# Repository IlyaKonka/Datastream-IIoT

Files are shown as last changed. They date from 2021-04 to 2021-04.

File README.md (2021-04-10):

# Data Stream Processing in IIoT environments
## Video demonstration
[](https://youtu.be/aPCmk4RJr00)
## Video description
At the top of the video you can see log output of IIoT-System.
There is vibration visualisation in the right corner and live video of the lego prototype in the left corner.<br>
<br>
<br>
Timecodes:
* (0:00 — 0:30) start of IIoT-System
* (0:30 — 0:52) response of **identification module** to the lego part without id tag 
* (0:54 — 2:53) production workflow of **defect 1** lego part 
* (1:30 — 1:45) demonstration of predictive maintenance
* (2:56 — 4:40) production workflow of **non-defective** lego part
* (4:45 — 5:00) transport to the **drop zone** the lego part which has already been processed

## Sensor simulators
You can start the docker project with vibration/color sensor simulator(s).
There is more information in the **IIoT-System** folder.

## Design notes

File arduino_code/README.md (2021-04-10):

# Arduino code
## Getting Started
Before use install libraries from libraries.7z

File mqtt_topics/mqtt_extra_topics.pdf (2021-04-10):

Loading

Topic | Type | Payload | Description
/tables/connection | Publish | arduinoLoadingTable|connected arduinoRollingTable|connected arduinoQualityTable|connected arduinoColourSensor|connected arduinoUnloadingTable|connected | Info about connection of the arduinos.
/loading/loopTime | Publish | {timeMillis} | Time of the main loop.
/loading/motorInfo | Publish | isStarted|{ value } direction|{value} speed|{value} | Info about motor. isStarted: 0 or 1 direction: l or r speed: (0,255)
/loading/info | Publish | isStarted|{ value } direction|{value} speed|{value} loopTime|{value} action|{value} DoneMsg | Info about table if something was changed. isStarted(motor): 0 or 1q direction: l or r speed: (0,255) loopTime: 0 or 1 action: F or D DoneMsg: “ Rolling is done.”
/loading/warning | Publish | Some warnings | If something wrong, Arduino sends a msg
/loading/rfidReadProblem | Publish | Msg with info about movement of the material. (a lit bit right or left) | If rfid reader cannot read a tag, this msg will be sent.
/loading/control | Subscribe | {t} – loop time (on/off) {i} – motorInfo {s} – start motor {p} – pause motor {r} – direction right {l} – direction left {number} – speed (0,255) | Extra control of the table. (GodMode)

Rolling

Topic | Type | Payload | Description
/rolling/loopTime | Publish | {timeMillis} | Time of the main loop.
/rolling/motorInfo | Publish | isStarted|{ value } isRollingStarted|{value} direction|{value} rollingDirection|{value} speed|{value} rollingSpeed|{value} | Info about motor. isStarted: 0 or 1 isRollingStarted| 0 or 1 direction: l or r rollingDirection: l or r speed: (0,255) rollingSpeed: (0,255)
/ rolling /info | Publish | isStarted|{ value } isRollingStarted|{value} direction|{value} rollingDirection|{value} speed|{value} rollingSpeed|{value} loopTime|{value} DoneMsg | Info about table if something was changed. isStarted(motor): 0 or 1 direction: l or r speed: (0,255) loopTime: 0 or 1
/ rolling /warning | Publish | Some warnings | If something wrong, Arduino sends a msg
/ rolling /control | Subscribe | {t} – loop time (on/off) {i} – motorInfo {s} – start motor {p} – pause motor {m} – start roll {z} – pause roll {r} – direction right (automatically for roll direction) {l} – direction left (automatically for roll direction) {number} – speed (0,255) (automatically for roll speed) | Extra control of the table. (GodMode)

Quality

Topic | Type | Payload | Description
/quality/loopTime | Publish | {timeMillis} | Time of the main loop.
/quality/motorInfo | Publish | isStarted|{ value } direction|{value} speed|{value} | Info about motor. isStarted: 0 or 1 direction: l or r speed: (0,255)
/quality/info | Publish | isStarted|{ value } direction|{value} speed|{value} loopTime|{value} DoneMsg | Info about table if something was changed. isStarted(motor): 0 or 1 direction: l or r speed: (0,255) loopTime: 0 or 1
/ quality /warning | Publish | Some warnings | If something wrong, Arduino sends a msg
/ quality /control | Subscribe | {t} – loop time (on/off) {i} – motorInfo {s} – start motor {p} – pause motor {r} – direction right {l} – direction left {number} – speed (0,255) | Extra control of the table. (GodMode)

ColourSensor

Topic | Type | Payload | Description
/ colourSensor/warning | Publish | Some warnings | If something wrong, Arduino sends a msg

Unloading

Topic | Type | Payload | Description
/unloading/loopTime | Publish | {timeMillis} | Time of the main loop.
/unloading/motorInfo | Publish | isStarted|{ value } direction|{value} speed|{value} TurnedOut|{value} | Info about motor. isStarted: 0 or 1 direction: l or r speed: (0,255) TurnedOut: 0 or 1 (position of turnout system [0 is start pos])
/ unloading /info | Publish | isStarted|{ value } direction|{value} speed|{value} loopTime|{value} TurnedOut|{value} DoneMsg | Info about table if something was changed. isStarted(motor): 0 or 1 direction: l or r speed: (0,255) loopTime: 0 or 1 TurnedOut: 0 or 1 (position of turnout system [0 is start pos])
/ unloading /warning | Publish | Some warnings | If something wrong, Arduino sends a msg
/ unloading /control | Subscribe | {t} – loop time (on/off) {i} – motorInfo {s} – start motor {p} – pause motor {r} – direction right {l} – direction left {number} – speed (0,255) {f} – turn out forward {b} – turn out back | Extra control of the table. (GodMode)

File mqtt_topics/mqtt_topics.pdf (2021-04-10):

### 1.1 Loading

### 1.1.1 MQTT messages

Name | P/S | Topic | Payload | QoS | Lvl | Description
ReadyToNewMat | Publish | /loading/ReadyToNewMat | String “ready” | 0 | 3 | Sends the messages if it is ready for the new material part. (interval 0.5 s)
MatLoaded | Publish | /loading/MatLoaded | String {MAT_ID} | 0 | 3 | Is send when a material is placed on the Roller Table and the RFID reader reads it. Contains the id of the material.
MatPosition | Publish | /loading/MatPosition | String {MAT_ID}|{MAT_POS} | 0 | 3 | Sends position of the material all the time when it is on the table.
MatLoadingInfo | Publish | /rolling/ MatLoadingInfo | String {MAT_ID} | 0 | 2 | Sends id if material is ready to roll.
MatDropped | Publish | /loading/ MatDropped | String {MAT_ID} | 0 | 3 | Msg after dropping.
MatProcess | Subscribe | /loading/MatProcess | String {MAT_ID}|F or {MAT_ID}|D | 1 | 3 | Waits for a message with the command from the server. There are two commands. “Forwarding” or “Dropping “.
MatReadyToRoll | Subscribe | /loading/MatReadyToRoll | String {MAT_ID} | 0 | 2 | Waits for the message from the rolling table (1.2) that it is ready.

### 1.2 Rolling

### 1.2.1 MQTT messages

Name | P/S | Topic | Payload | QoS | Lvl | Description
MatReadyToRoll | Publish | /loading/MatReadyToRoll | String {MAT_ID} | 0 | 2 | Sends the messages if it is ready for the new material part.
MatPosition | Publish | /rolling /MatPosition | String {MAT_ID}|{ MAT_POS} | 0 | 3 | Sends position of the material all the time when it is on the table.
RollQuery | Publish | /rolling / RollQuary | String {MAT_ID} | 0 | 3 | Sends id of material (before rolling).
MatRollInfo | Publish | /quality / MatRollInfo | String {MAT_ID} | 0 | 2 | Sends id if material is ready to quality check.
MatAfterRoll | Publish | rolling/ MatAfterRoll | String {MAT_ID} | 0 | 3 | Msg after roll
RollThickness | Subscribe | /rolling/ RollThickness | String {MAT_ID}|{ MAT_THKN SS} | 1 | 3 | After RollQuery server sends info about thickness of the material. Then it can be rolled in some mode of the roller table.
MatLoadingInfo | Subscribe | /rolling/ MatLoadingInfo | String {MAT_ID} | 0 | 2 | Waits for the message with information about id. (from Loading Table) Then motor is started and transport material to the “Roll”.
MatReadyToQCh eck | Subscribe | /rolling/ MatReadyToQCheck | String {MAT_ID} | 0 | 2 | Waits for the message from the quality table (1.3) that it is ready.

### 1.3 Quality

### 1.3.1 MQTT messages

Name | P/S | Topic | Payload | QoS | Lvl | Description
MatReadyToQCheck | Publish | /rolling/MatReadyToQCheck | String {MAT_ID} | 0 | 2 | Sends the messages if it is ready for the new material part.
MatPosition | Publish | /quality/MatPosition | String {MAT_ID}|{M AT_POS} | 0 | 3 | Sends position of the material all the time when it is on the table.
MatReadyToQCheck | Publish | / quality / MatReadyToQCheck | String {MAT_ID} | 0 | 2/3 | Sends the message to server (colour sensor) when the material is in the “quality check place”.
MatQualityInfo | Publish | /unloading/MatQualityInfo | String {MAT_ID} | 0 | 2 | Sends id if material is ready to unloading.
MatRollInfo | Subscribe | /quality/ MatRollInfo | String {MAT_ID} | 0 | 2 | Waits for the message with information about id. (from Rolling Table) Then motor is started and transport material to the colour sensor.
MatCheck | Subscribe | /quality/ MatCheck | String {MAT_ID}|{RS LT} | 0 | 2/3 | Waits for server callback with result of qcheck. After the signal the material will be moved to the end of the quality table.
MatReadyToUnloading | Subscribe | /quality/MatReadyToUnloading | String {MAT_ID} | 0 | 2 | Waits for the message from the unloading table (1.4) that it is ready.
MatMove | Subscribe | /quality/MatMove | String {MAT_ID} | 0 | 2 | Waits for the message from the colour sensor (if it is connected) and then move material forward and back to detect a defect.

### 1.3.2 Colour Sensor

Name | P/S | Topic | Payload | QoS | Lvl | Description
MatCheck | Publish | /colourSensor/MatCheck | String {MAT_ID}| | 0 | 3 | Sends byte arr. Size=400 First 8 byte is id of mat (ascii) Then r,g,b [0,255] If it is not enough time for colour sensor to fill all arr, it fills automatically with 0.
MatMove | Publish | /quality/MatMove | String {MAT_ID}|s {MAT_ID}|e | 0 | 2 | Sends msg to the quality table that the material should be moved. (to detect little defects) at first s (start pos) And then e (end pos)
MatReadyToQCheck | Subscribe | /colourSensor/MatReadyToQCh eck | String {MAT_ID} | 0 | 3 | Waits for the message from the server then start communication with quality table.
StartAutoQCheck | Subscribe | /colourSensor/StartAutoQCheck | String {MAT_ID} | 0 | 2 | Waits for the msg from quality table and only then colour sensor works.
MatEndQCheck | Subscribe | /colourSensor/MatEndQCheck | String {MAT_ID} | 0 | 2 | Waits for the message from the quality table that the moving of material is finished, then colour sensor stops.

Unloading

### 1.3.3 MQTT messages

Name | P/S | Topic | Payload | QoS | Lvl | Description
MatReadyToUnlo ading | Publish | /quality/ MatReadyToUnloading | String {MAT_ID} | 0 | 2 | Sends the messages if it is ready for the new material part.
MatPosition | Publish | /unloading/MatPosition | String {MAT_ID}|{ MAT_POS} | 0 | 3 | Sends position of the material all the time when it is on the table.
MatFinal | Publish | /unloading/ MatFinal | String {MAT_ID} | 0 | 3 | Sends when the material is finally handled and transported.
MatQuery | Publish | /unloading/ MatQuery | String {MAT_ID} | 0 | 3 | Sends id of material (before rolling).
MatDrop | Subscribe | /unloading/MatDrop | String {MAT_ID}|1 or {MAT_ID}|0 | 1 | 3 | Waits for the message (after MatQuery) from the server with information about quality test. If it is ok, then continue rolling. If not, it will be turned out.
MatQualityInfo | Subscribe | /unloading/MatQualityIn fo | String {MAT_ID} | 0 | 2 | Waits for the message with information about id. (from Quality Table) Then motor is started and transport material to the “Turn out”.

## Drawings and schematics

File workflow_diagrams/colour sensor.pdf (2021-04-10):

# Colour Sensor

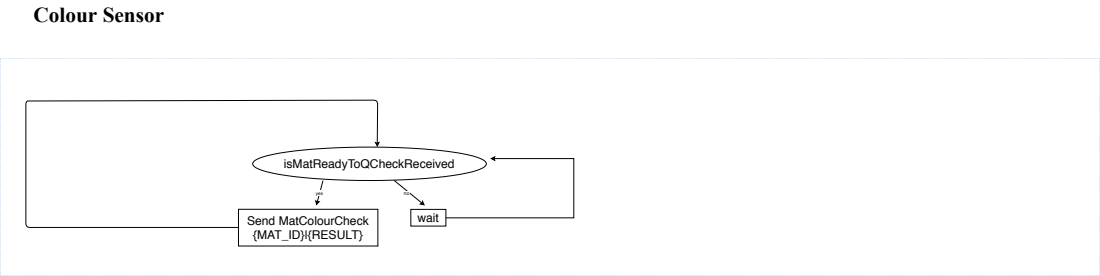
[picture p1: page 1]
isMatReadyToQCheckReceived; yes; Send MatColourCheck; wait; {MAT_ID}|{RESULT}

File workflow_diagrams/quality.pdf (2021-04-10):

# 3) Quality

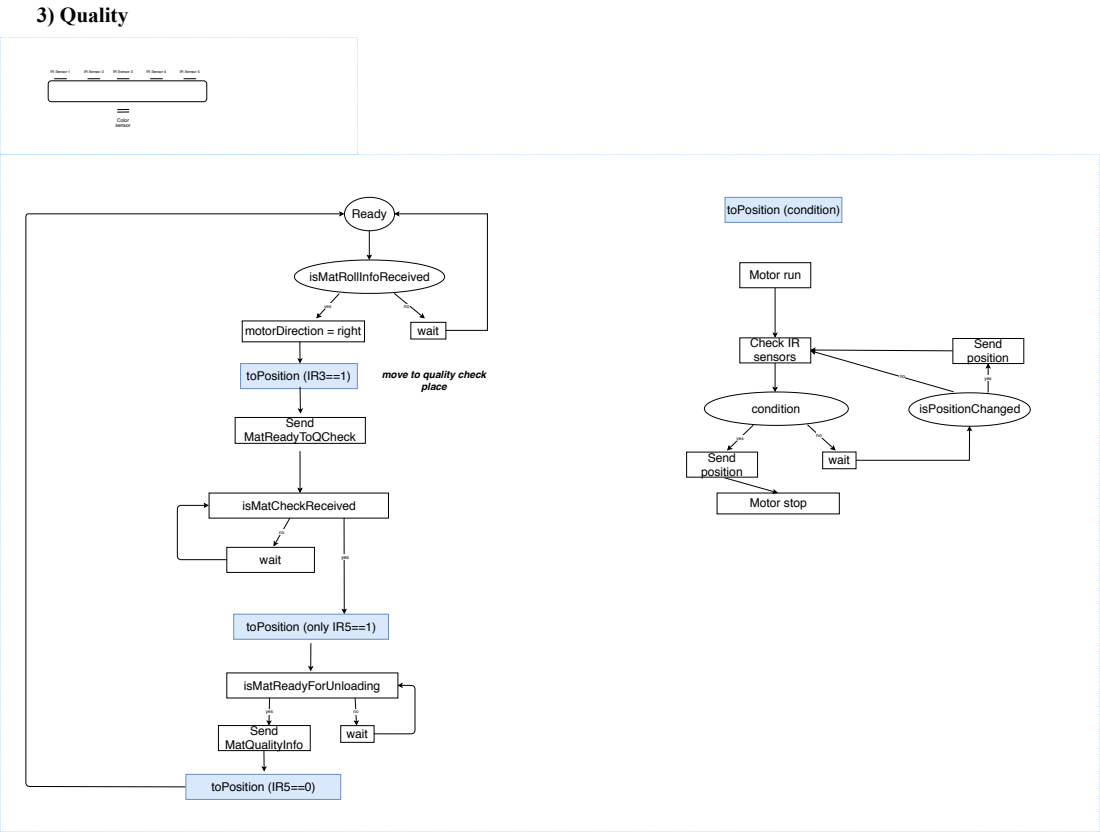
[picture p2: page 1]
IR Sensor 1; IR Sensor 2; IR Sensor 3; IR Sensor 4; IR Sensor 5; Ready; isMatRollInfoReceived; yes; wait; isMatReadyForUnloading; Color sensor; motorDirection = right; Send MatQualityInfo; Motor run; Motor stop; Check IR sensors; condition; Send position; isPositionChanged; toPosition (condition); toPosition (IR3==1); move to quality check; place; toPosition (only IR5==1); toPosition (IR5==0); isMatCheckReceived; yes wait; Send MatReadyToQCheck

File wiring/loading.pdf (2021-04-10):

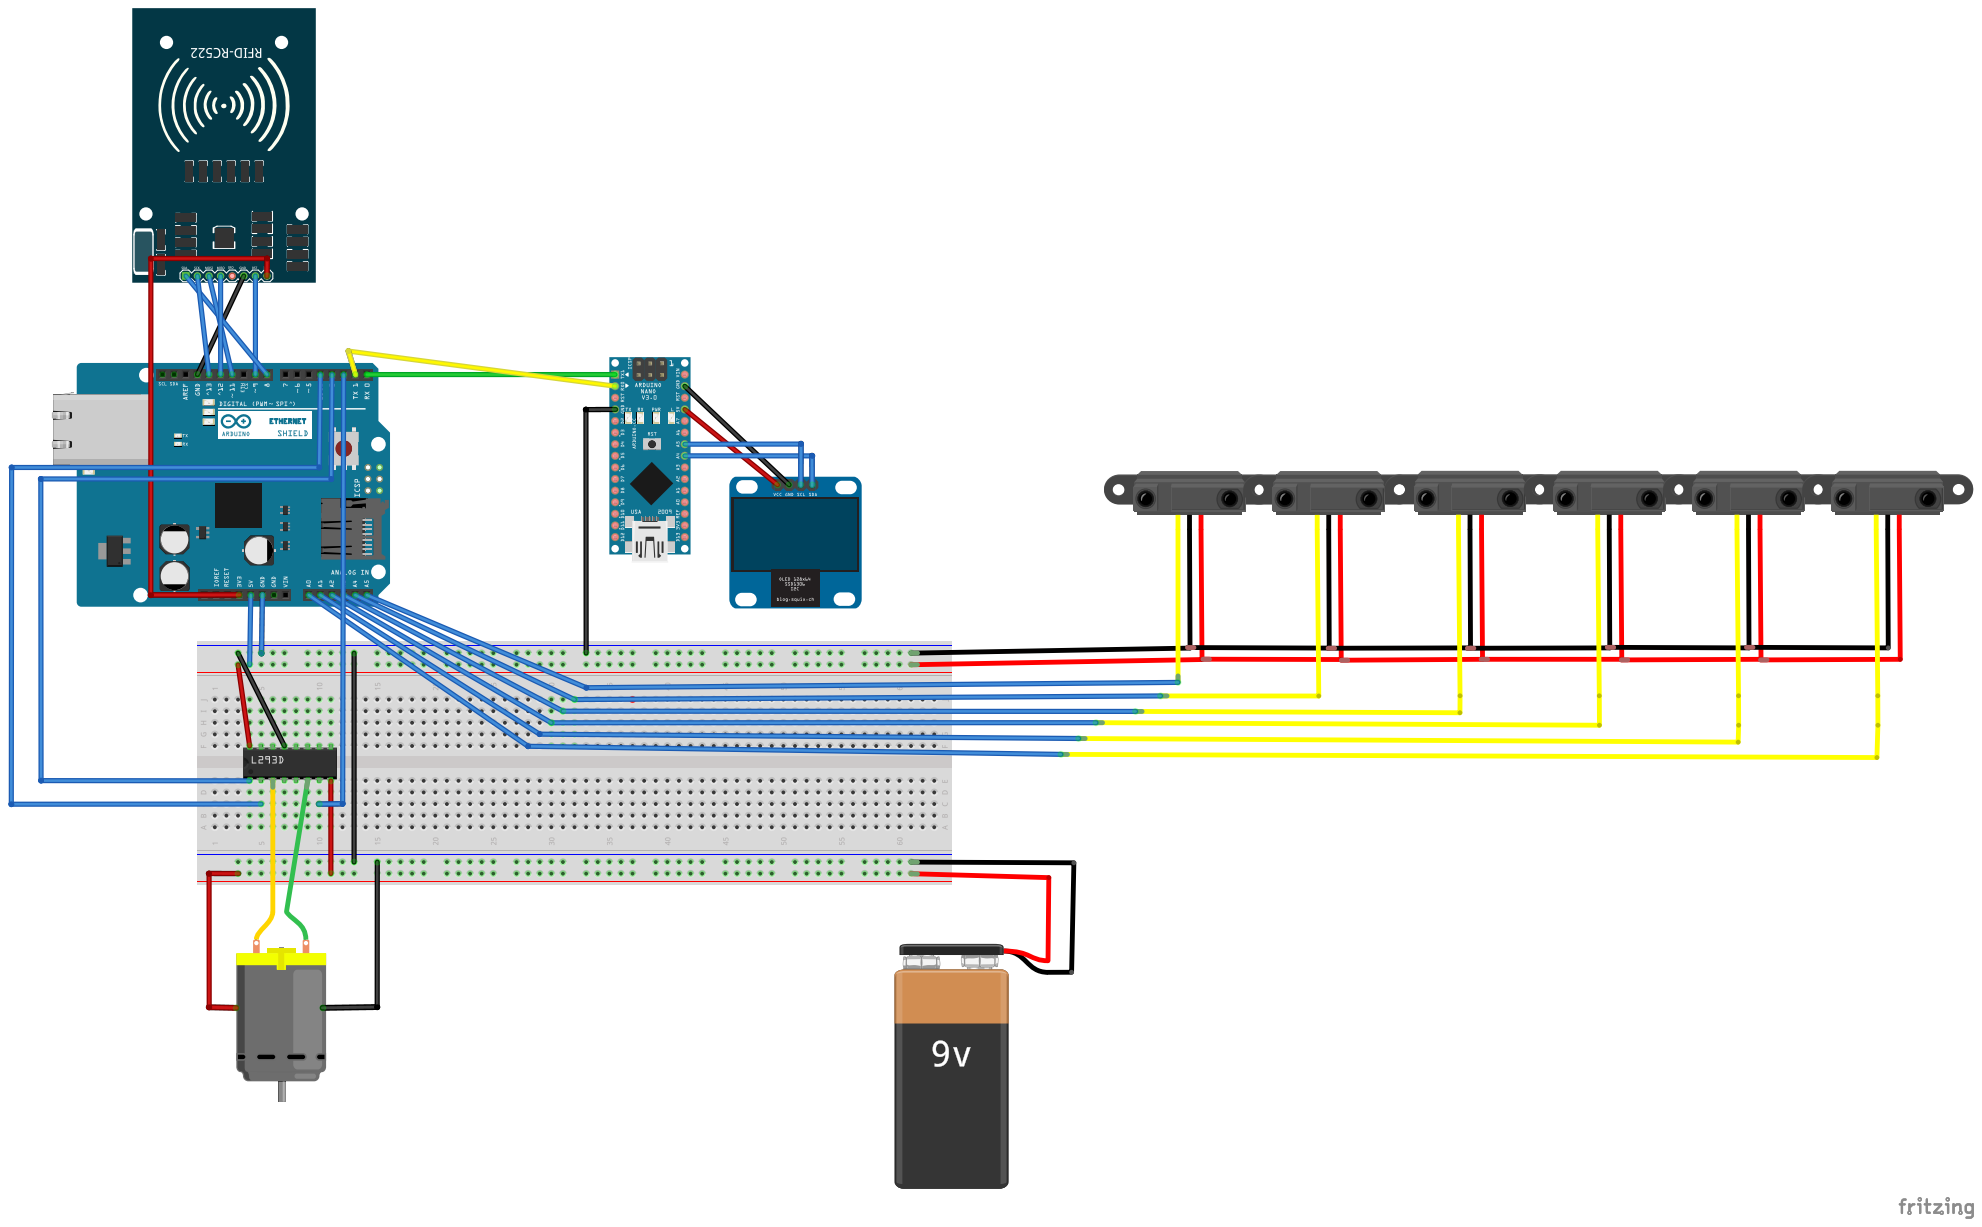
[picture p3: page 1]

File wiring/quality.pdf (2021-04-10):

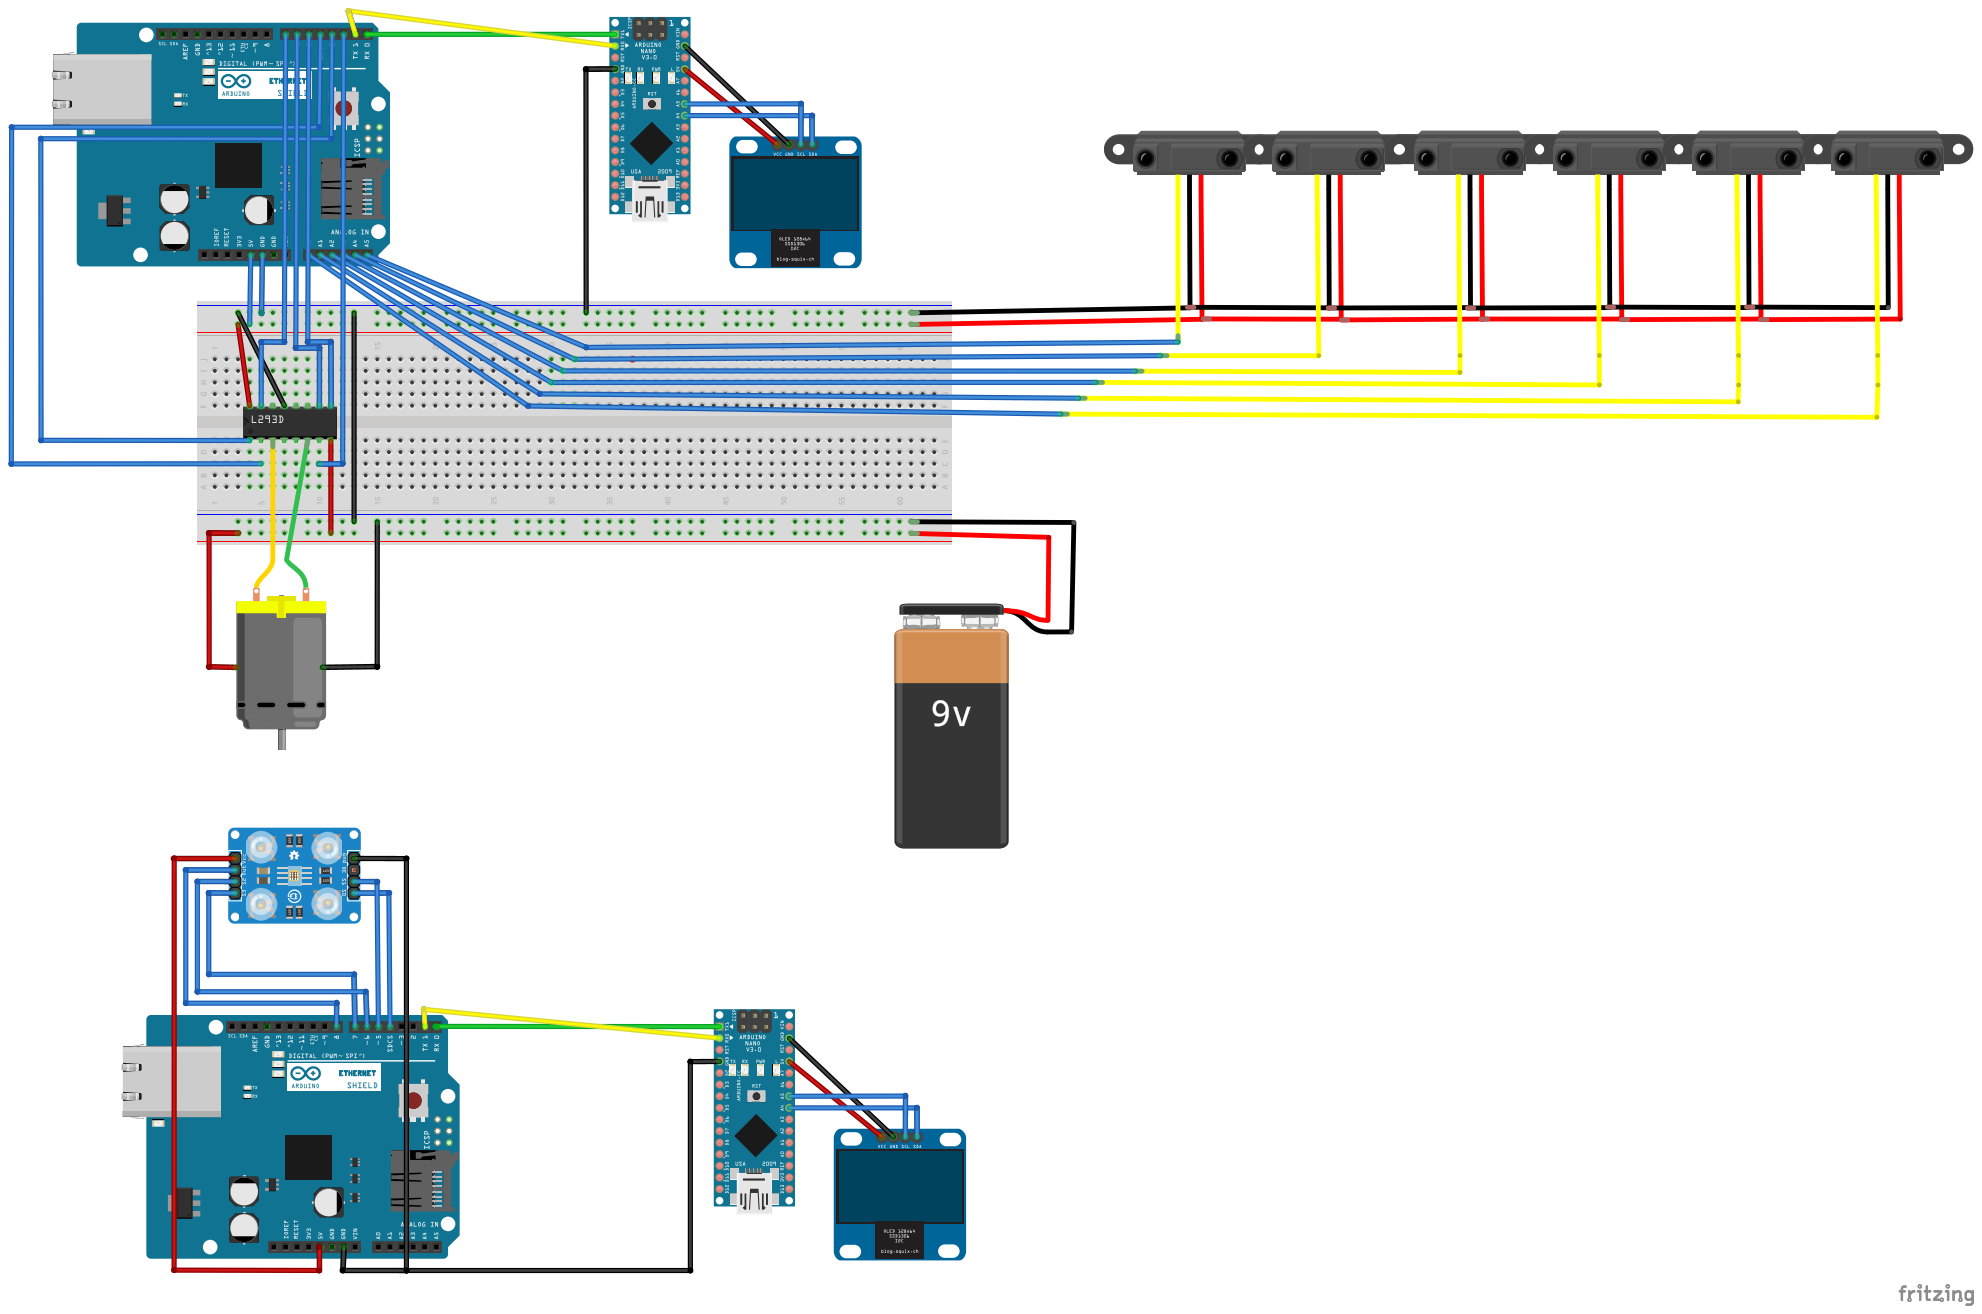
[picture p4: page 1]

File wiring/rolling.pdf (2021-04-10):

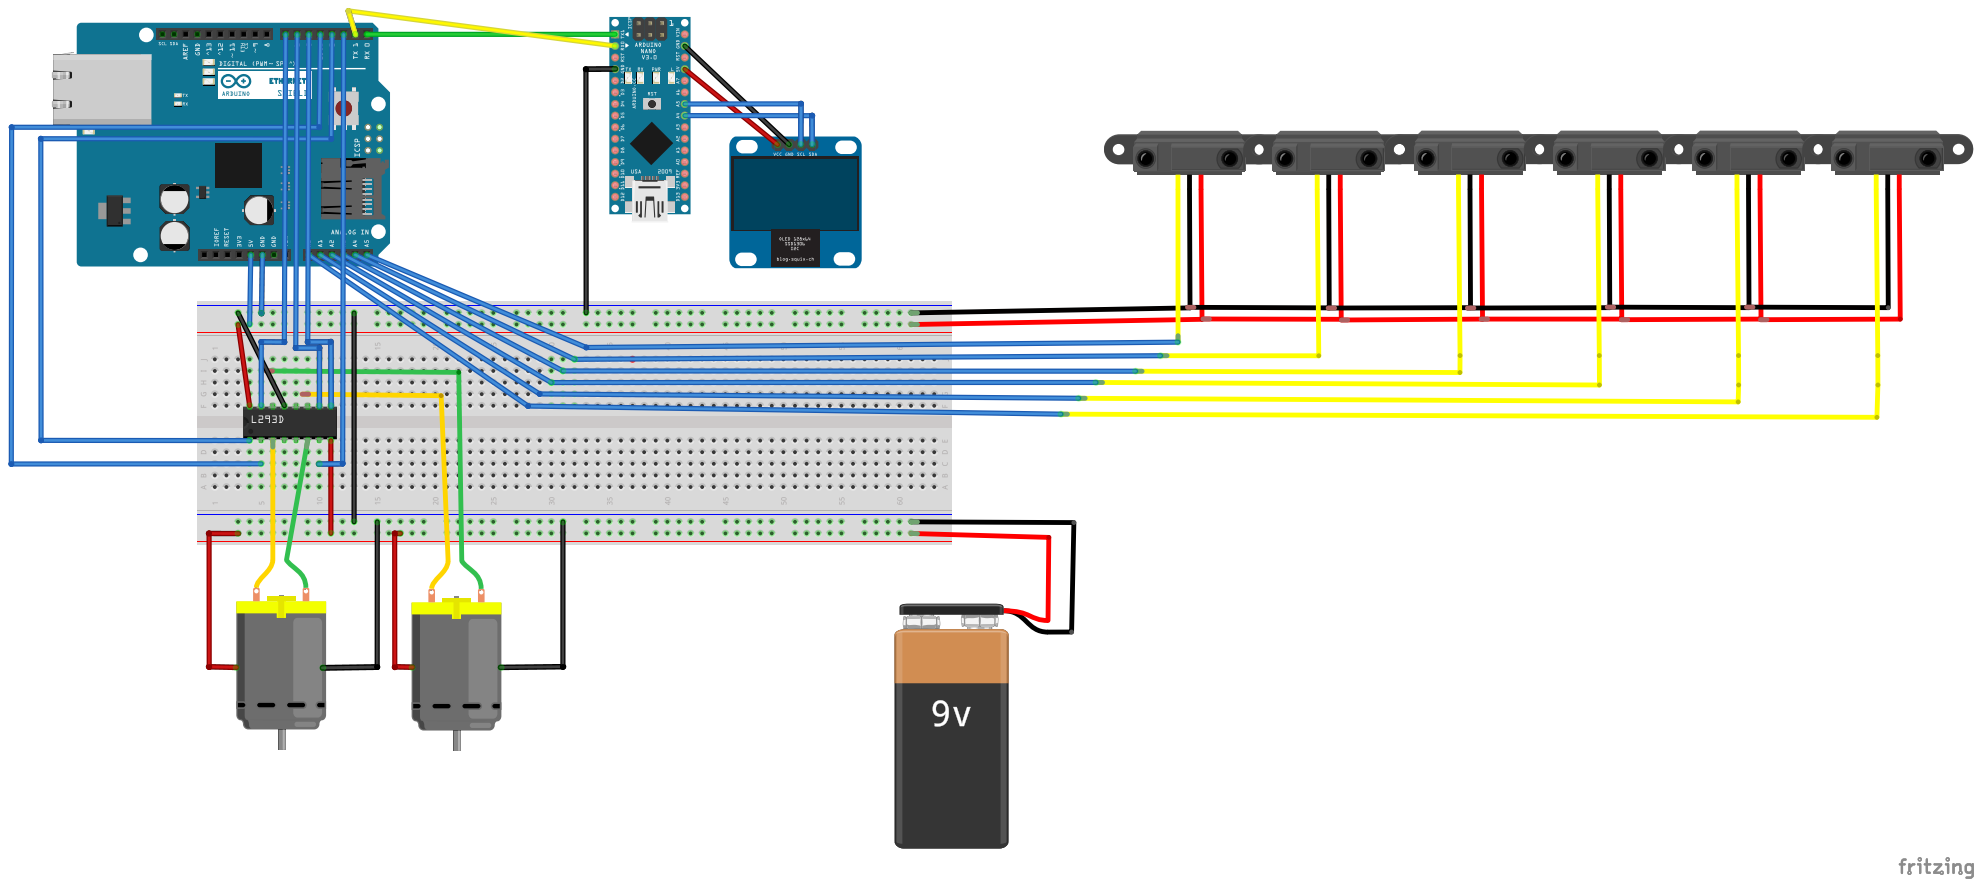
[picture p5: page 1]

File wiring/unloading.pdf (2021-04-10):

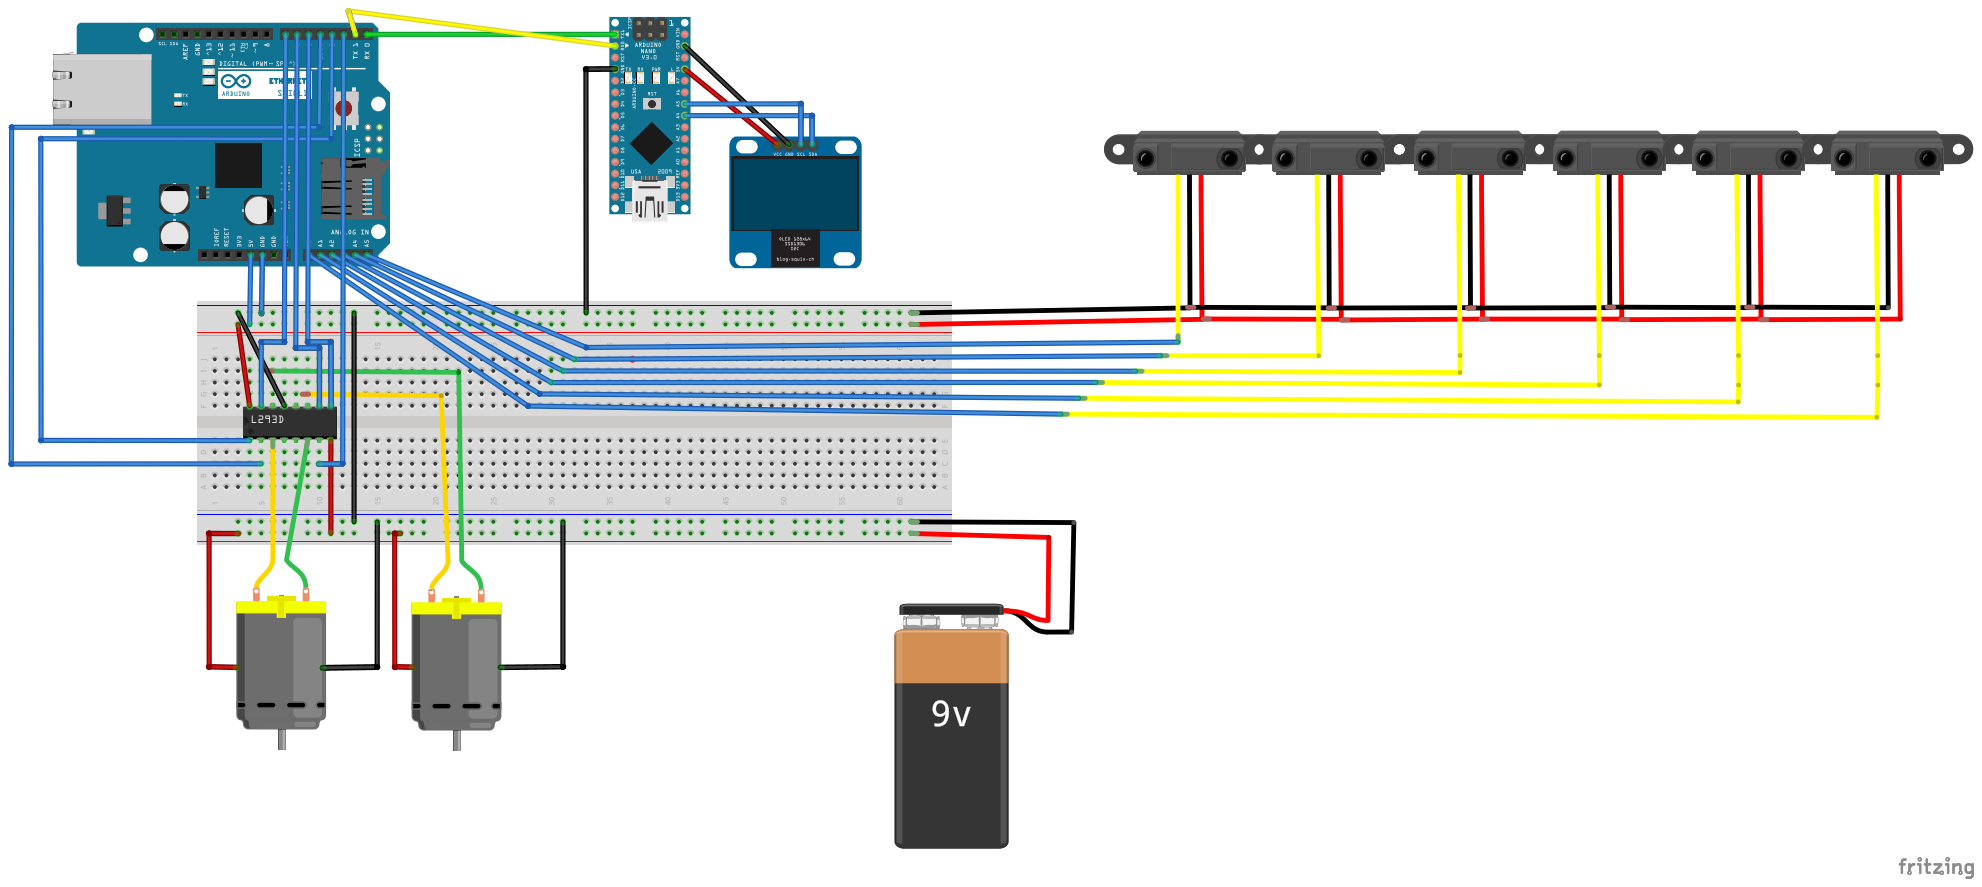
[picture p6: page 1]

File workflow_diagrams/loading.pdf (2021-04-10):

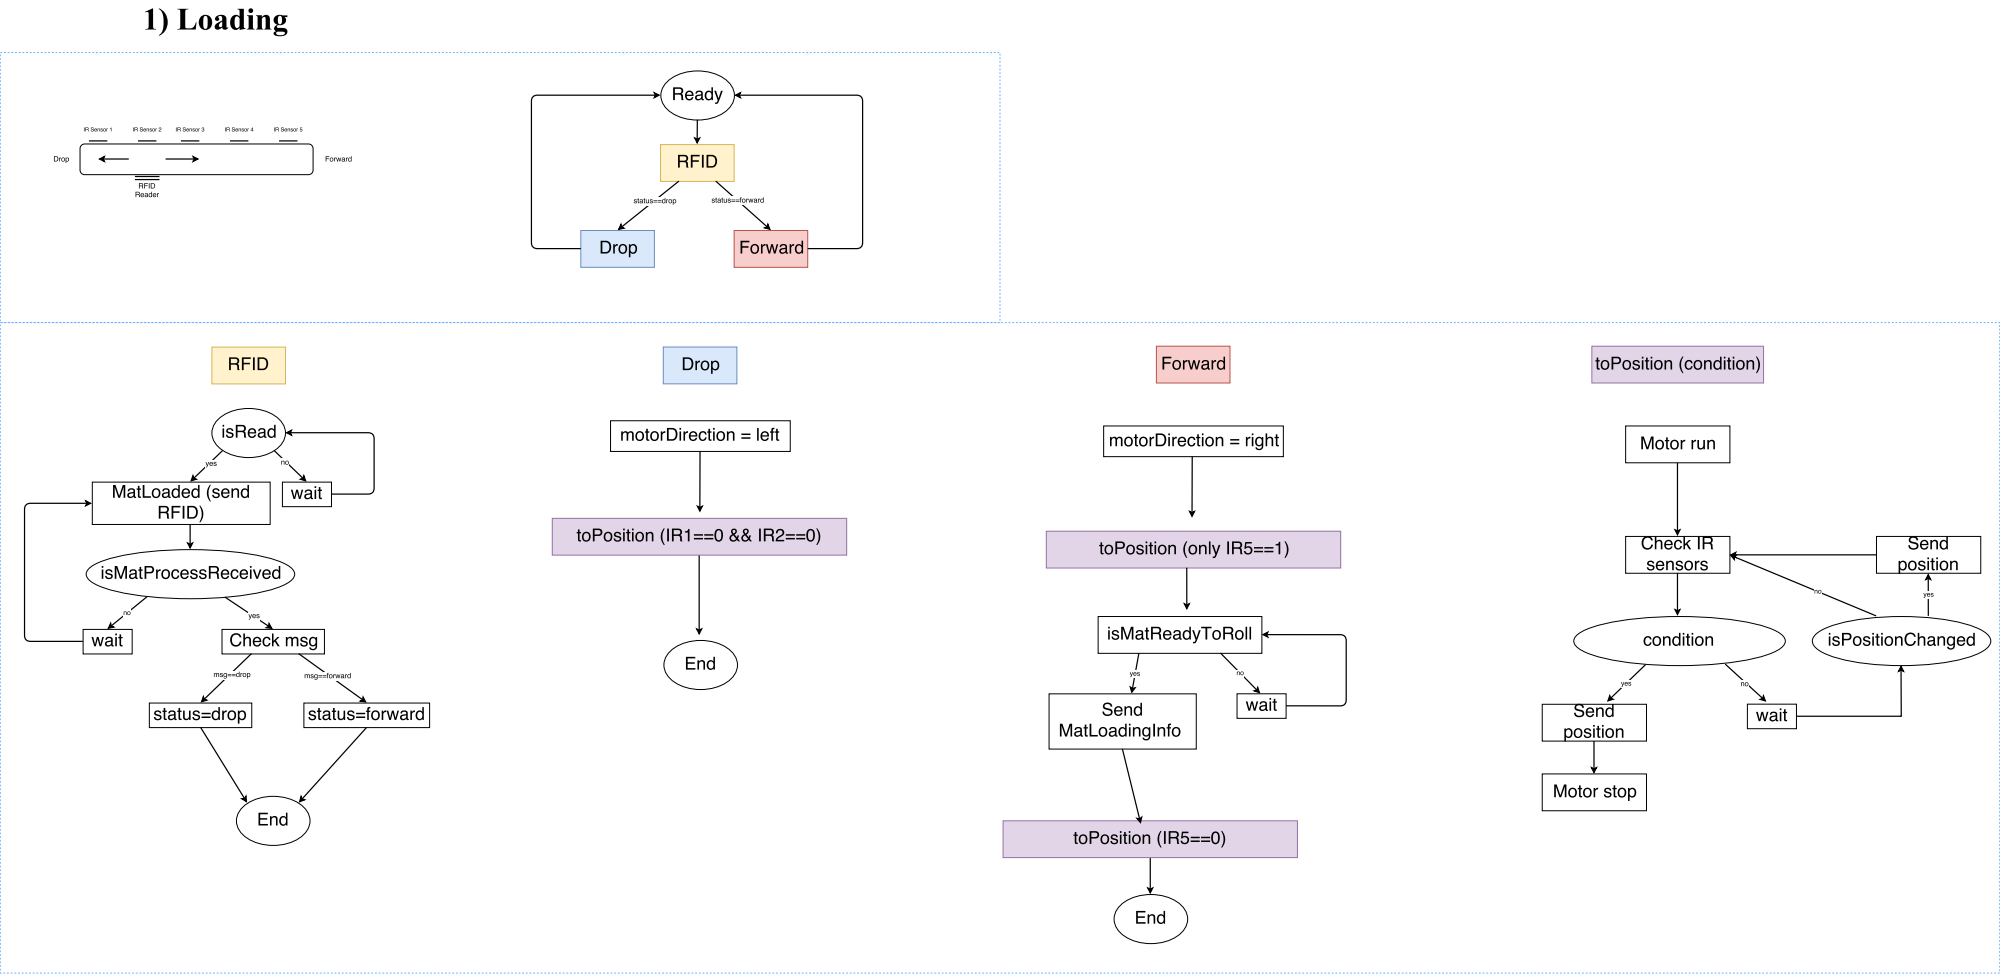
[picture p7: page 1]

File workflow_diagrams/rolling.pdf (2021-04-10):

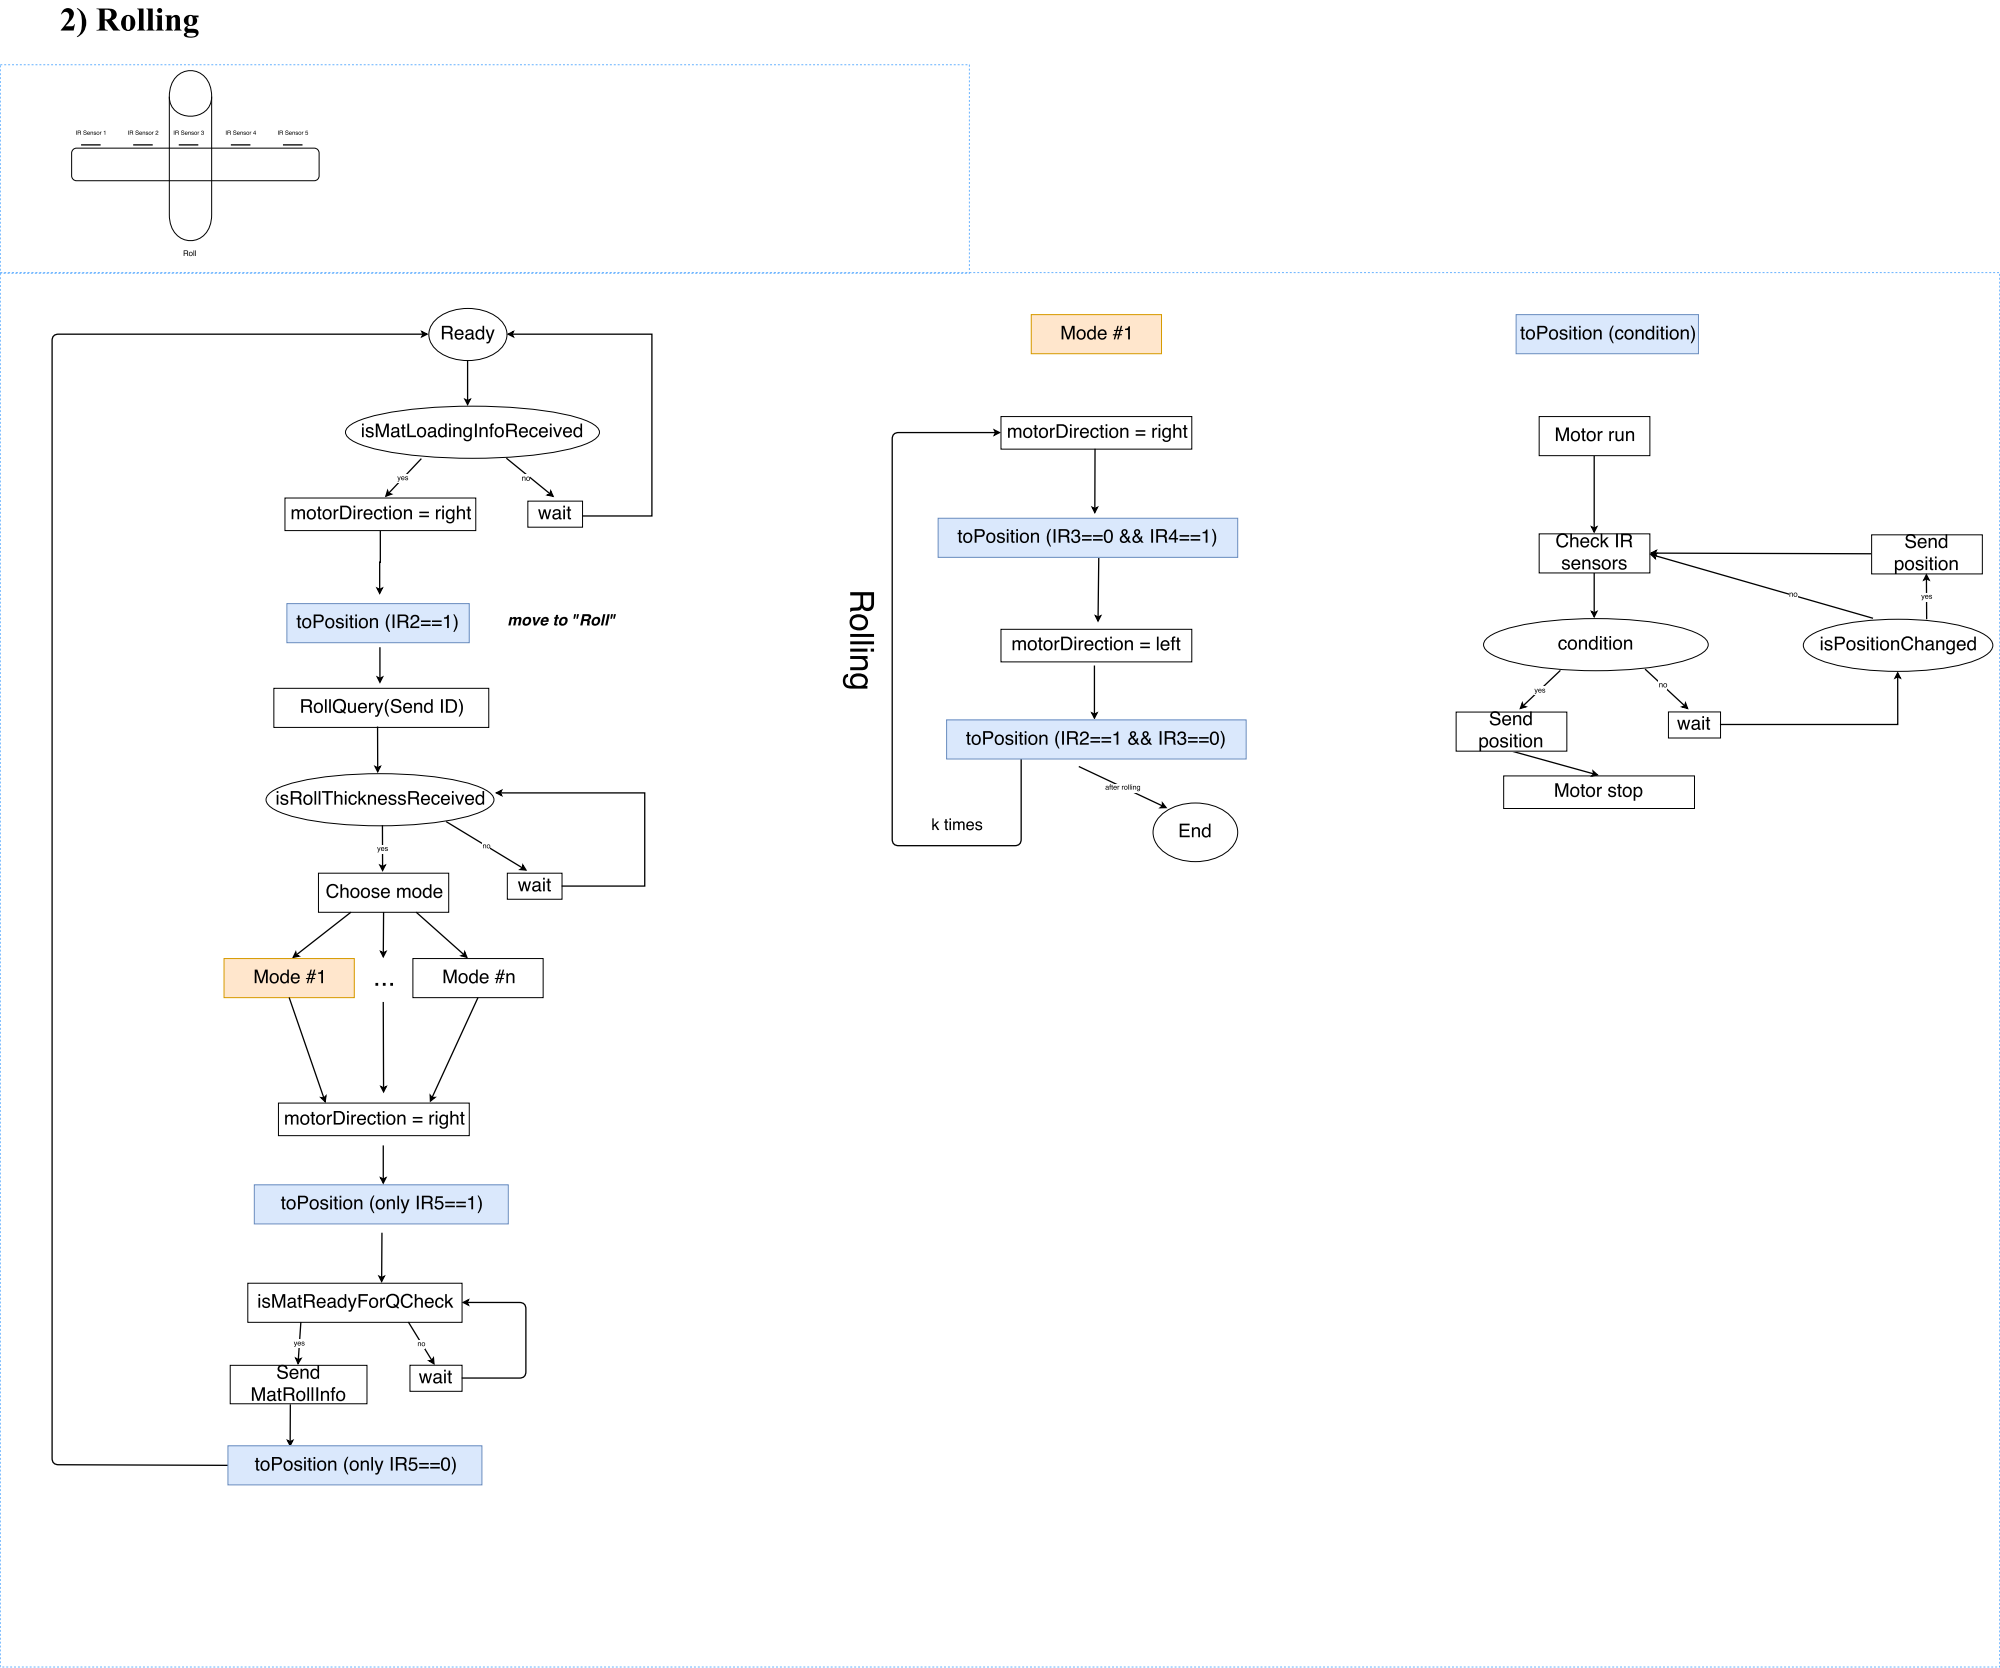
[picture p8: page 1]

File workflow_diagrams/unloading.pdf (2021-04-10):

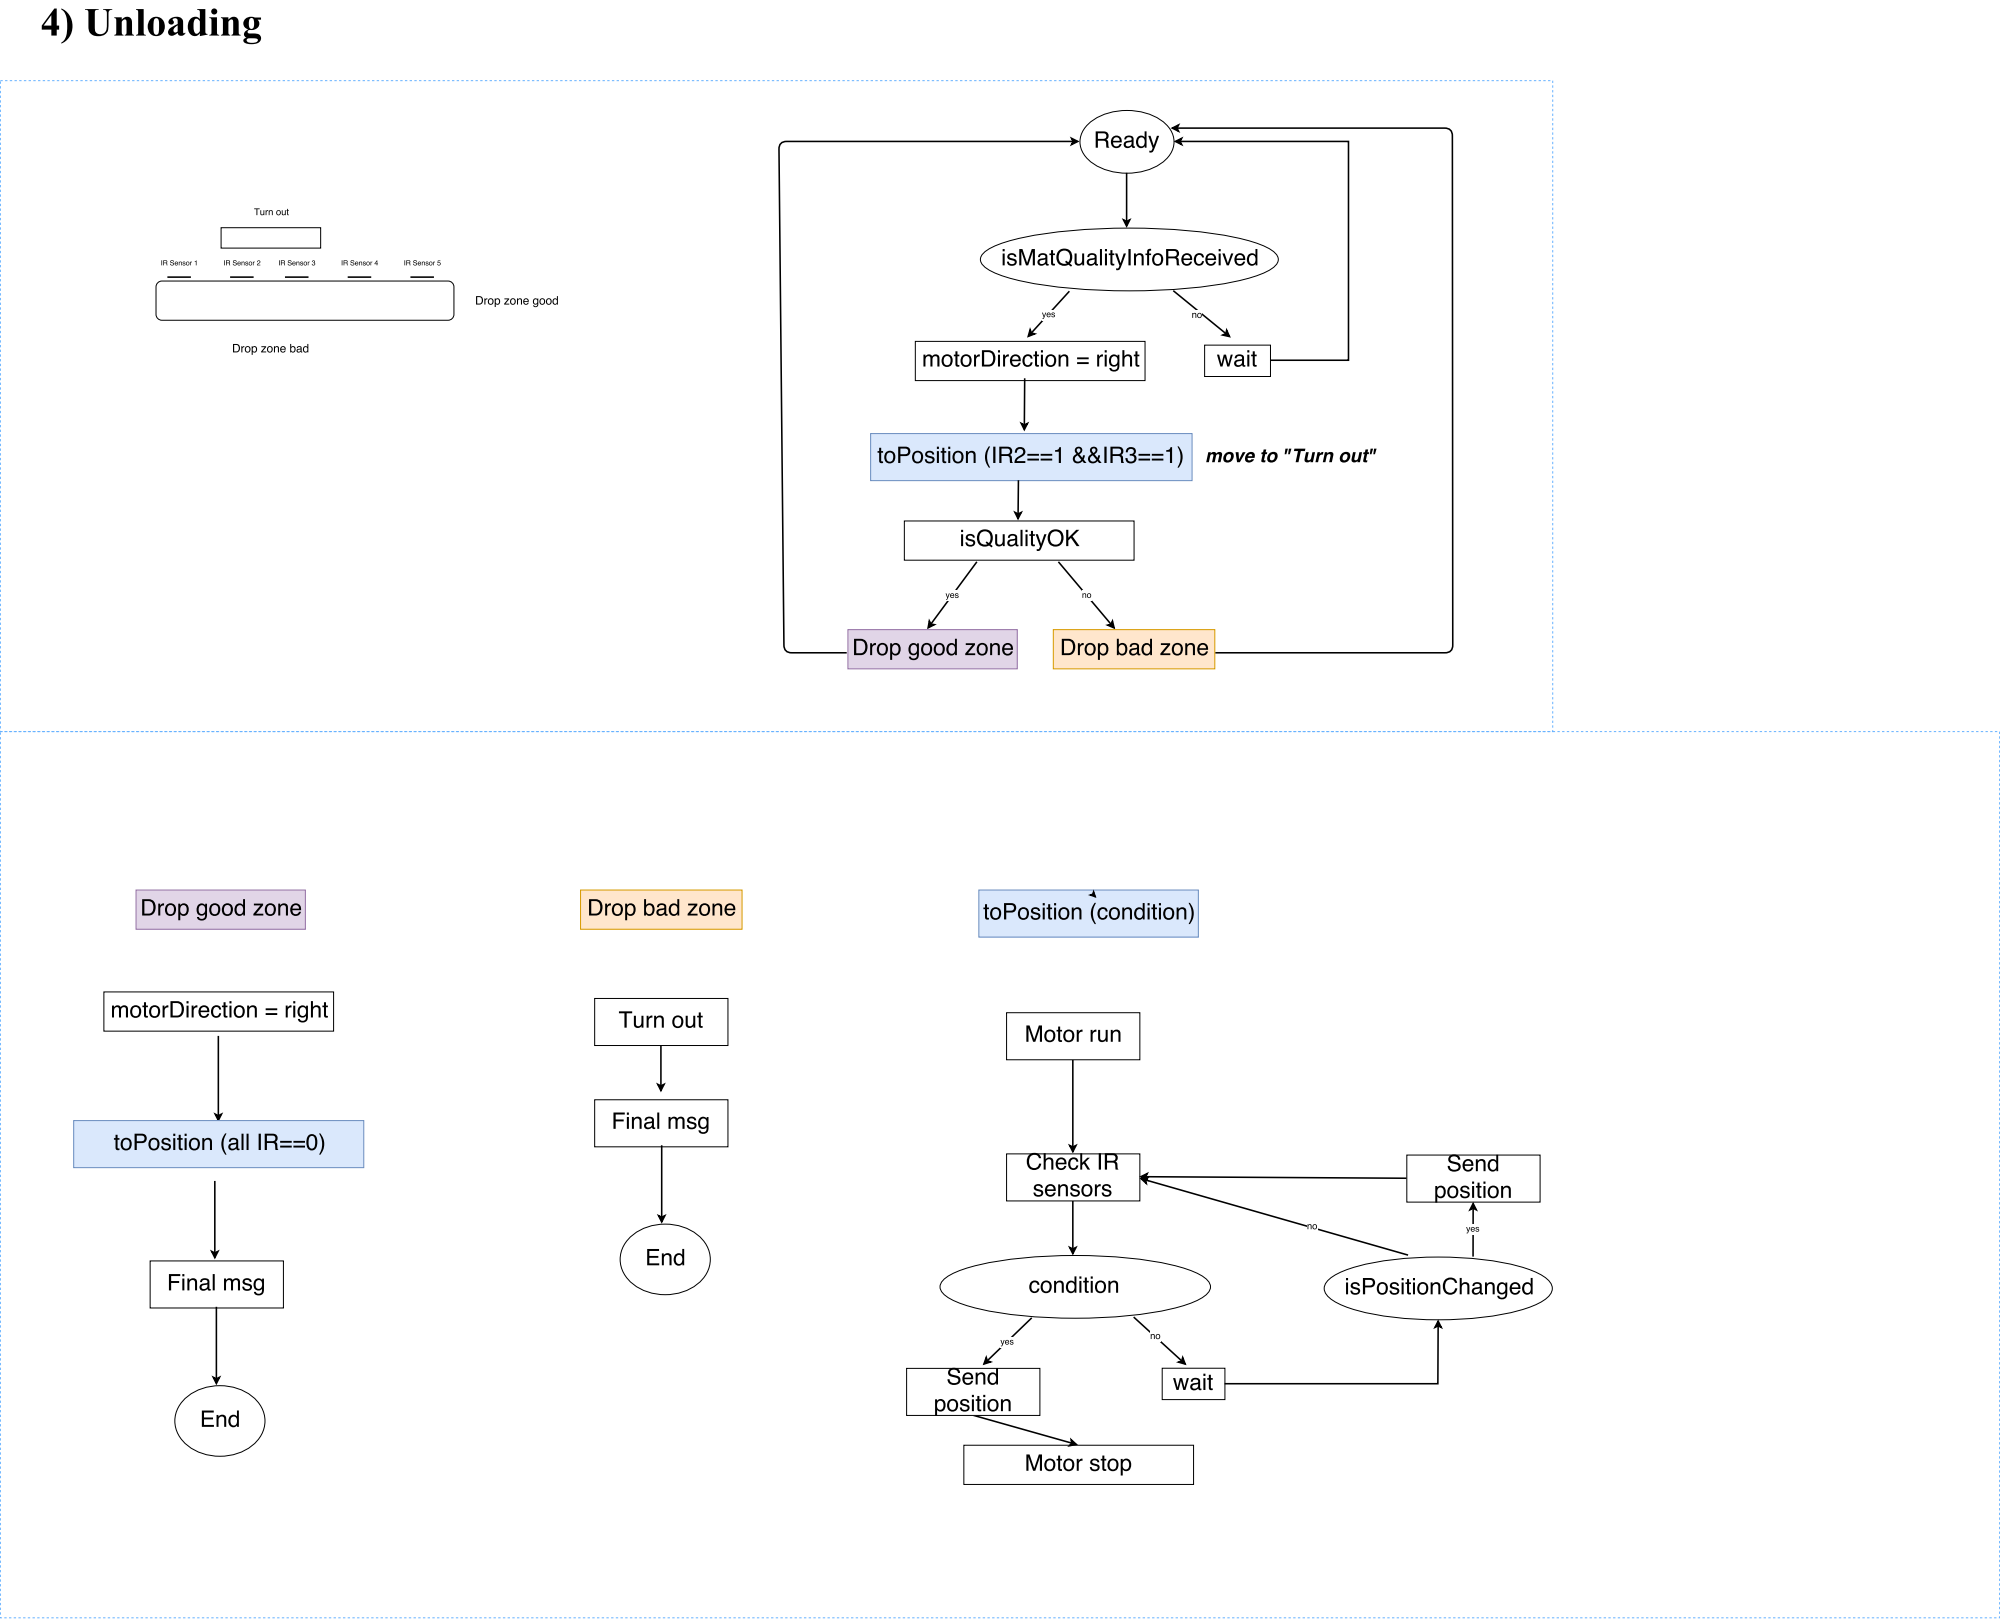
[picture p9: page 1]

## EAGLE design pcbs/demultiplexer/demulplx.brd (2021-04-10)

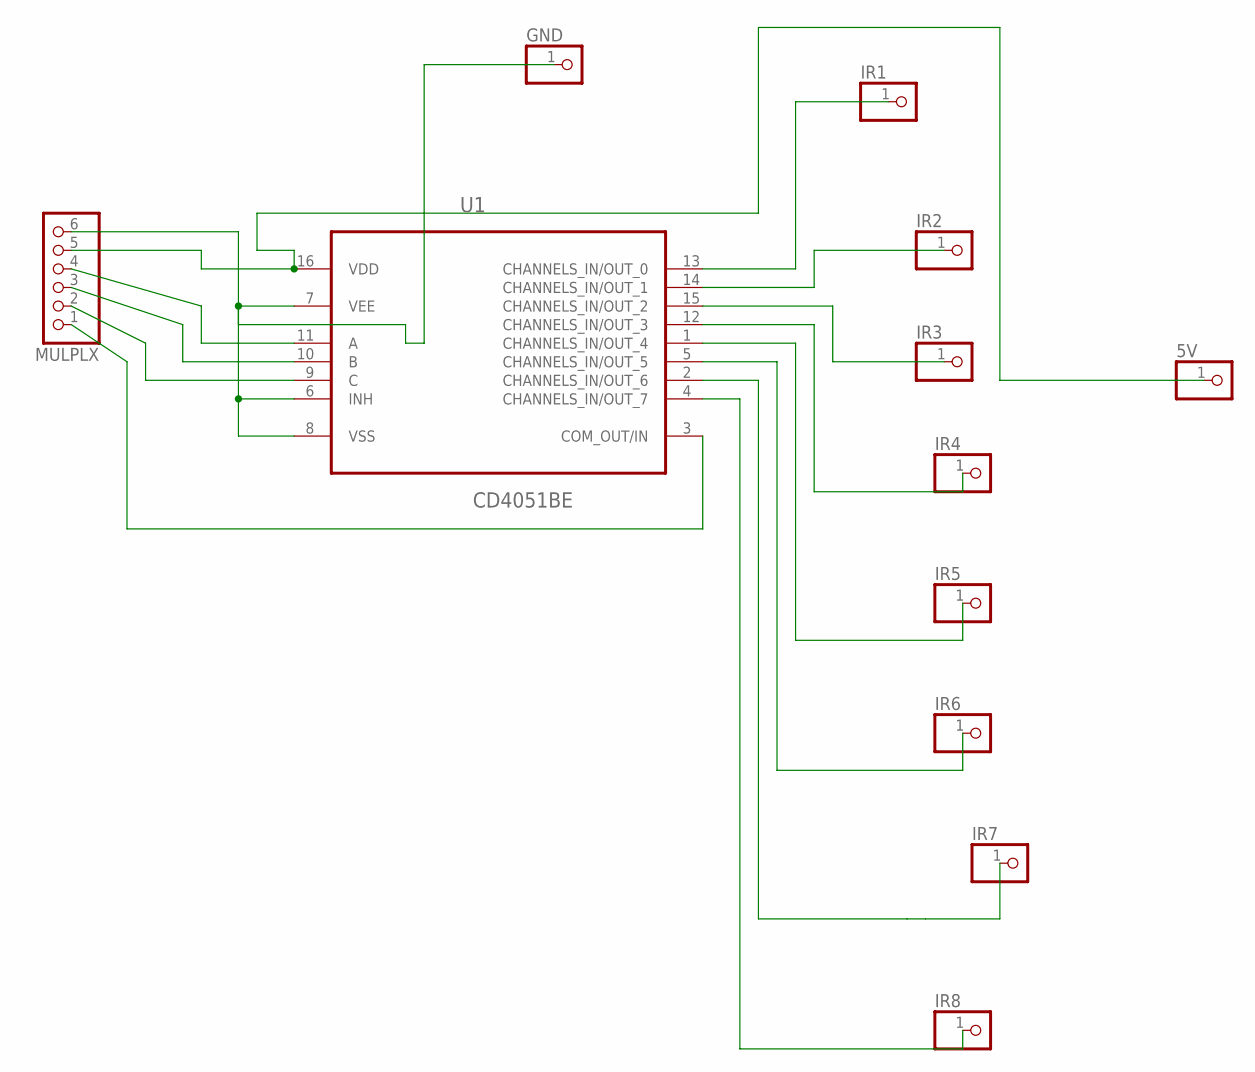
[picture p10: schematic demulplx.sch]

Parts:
5V: PINHD-1X01_2.54; 1X01
GND: PINHD-1X01_2.54; 1X01
IR1, IR2, IR3, IR4, IR5, IR6, IR7, IR8: PINHD-1X01_2.54; 1X01
MULPLX: PINHD-1X06_2.54-S; 1X06-S
U1: CD4051BE; DIP254P762X508-16

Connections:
5V: 5V.1, MULPLX.5, U1.16 (VDD)
GND: GND.1, MULPLX.6, U1.6 (INH), U1.7 (VEE), U1.8 (VSS)
unnamed: IR7.1, U1.2 (CHANNELS_IN/OUT_6)
unnamed: IR1.1, U1.13 (CHANNELS_IN/OUT_0)
unnamed: IR2.1, U1.14 (CHANNELS_IN/OUT_1)
unnamed: IR3.1, U1.15 (CHANNELS_IN/OUT_2)
unnamed: IR4.1, U1.12 (CHANNELS_IN/OUT_3)
unnamed: IR5.1, U1.1 (CHANNELS_IN/OUT_4)
unnamed: IR6.1, U1.5 (CHANNELS_IN/OUT_5)
unnamed: IR8.1, U1.4 (CHANNELS_IN/OUT_7)
unnamed: MULPLX.1, U1.3 (COM_OUT/IN)
unnamed: MULPLX.4, U1.11 (A)
unnamed: MULPLX.3, U1.10 (B)
unnamed: MULPLX.2, U1.9 (C)

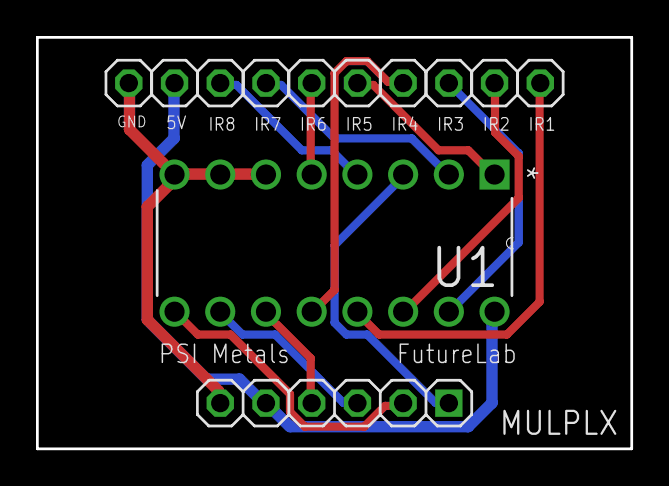
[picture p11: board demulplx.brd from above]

Board: 2 copper layers, 33.0 x 22.9 mm, 12 parts (0 on the bottom side), 14 nets.

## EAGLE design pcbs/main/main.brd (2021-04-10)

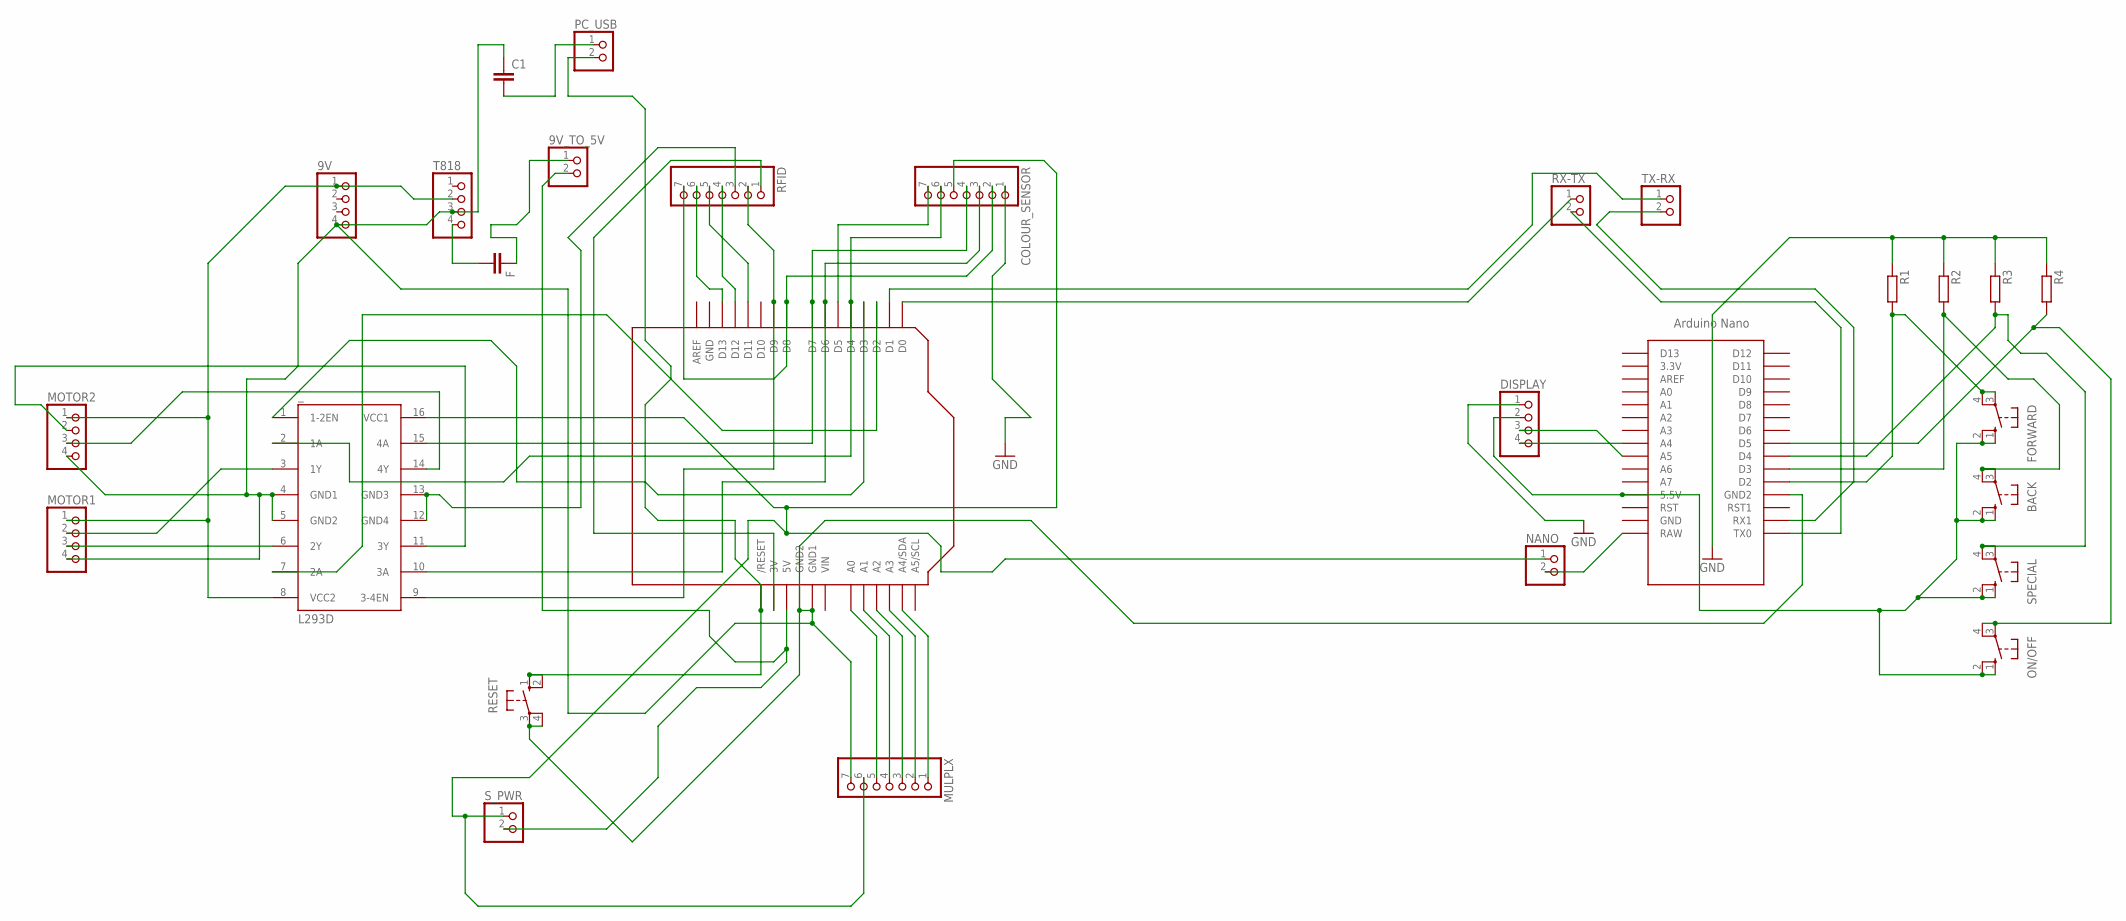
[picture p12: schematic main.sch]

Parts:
9V: PINHD-1X04_2.54-S; 1X04-S
9V_TO_5V: PINHD-1X02_2.54-S; 1X02-S
BACK: 10-XX; B3F-10XX
C1: C5/7.2; C5B7.2
COLOUR_SENSOR: PINHD-1X07_2.54-S; 1X07-S
DISPLAY: PINHD-1X04_2.54-S; 1X04-S
F: CC4532; C4532
FORWARD: 10-XX; B3F-10XX
MOTOR1, MOTOR2: PINHD-1X04_2.54-S; 1X04-S
MULPLX: PINHD-1X07_2.54-S; 1X07-S
NANO: PINHD-1X02_2.54-S; 1X02-S
ON/OFF: 10-XX; B3F-10XX
PC_USB: PINHD-1X02_2.54-S; 1X02-S
R1, R2, R3, R4: R-EU_R0805; R0805
RESET: 10-XX; B3F-10XX
RFID: PINHD-1X07_2.54-S; 1X07-S
RX-TX: PINHD-1X02_2.54-S; 1X02-S
SPECIAL: 10-XX; B3F-10XX
S_PWR: PINHD-1X02_2.54-S; 1X02-S
T818: PINHD-1X04_2.54-S; 1X04-S
TX-RX: PINHD-1X02_2.54-S; 1X02-S
U1: ARDUINOR3-DIMENSION; ARDUINOR3
U$1: NANO
_: L293D; DIL16

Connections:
GND: 9V.4, C1.1, COLOUR_SENSOR.1, DISPLAY.1, MOTOR1.4, MOTOR2.4, MULPLX.7, R1.1, R2.1, R3.1, R4.1, RESET.3, RESET.4 (P1), T818.3, U1.GND, U1.GND1, U1.GND2, U$1.GND1 (GND2), _.4 (GND1), _.5 (GND2)
unnamed: RFID.3, _.12 (GND4), _.13 (GND3)
unnamed: F.2, T818.4
unnamed: 9V_TO_5V.2, S_PWR.2, U1.5V
unnamed: COLOUR_SENSOR.2, RFID.7, U1.D8
unnamed: MULPLX.1, U1.A4 (A4/SDA)
unnamed: MULPLX.5, U1.A0
unnamed: MULPLX.4, U1.A1
unnamed: MULPLX.3, U1.A2
unnamed: MULPLX.2, U1.A3
unnamed: ON/OFF.3, ON/OFF.4 (P1), R4.2, U$1.D5
unnamed: COLOUR_SENSOR.7, U1.D5
unnamed: BACK.1 (S), BACK.2 (S1), DISPLAY.2, FORWARD.1 (S), FORWARD.2 (S1), ON/OFF.1 (S), ON/OFF.2 (S1), SPECIAL.1 (S), SPECIAL.2 (S1), U$1.5V (5.5V)
unnamed: PC_USB.2, RESET.1 (S), RESET.2 (S1), U1.RESET (/RESET)
unnamed: DISPLAY.3, U$1.A5
unnamed: DISPLAY.4, U$1.A4
unnamed: C1.2, PC_USB.1
unnamed: COLOUR_SENSOR.6, U1.D4, _.2 (1A)
unnamed: 9V.1, MOTOR1.1, MOTOR2.1, T818.2, _.8 (VCC2)
unnamed: RFID.1, U1.3V
unnamed: FORWARD.3, FORWARD.4 (P1), R1.2, U$1.D2
unnamed: RX-TX.1, U1.D0
unnamed: RX-TX.2, U$1.TX0
unnamed: TX-RX.1, U1.D1
unnamed: TX-RX.2, U$1.RX1
unnamed: NANO.2, U$1.RAW
unnamed: BACK.3, BACK.4 (P1), R2.2, U$1.D3
unnamed: RFID.2, U1.D9, _.9 (3-4EN)
unnamed: R3.2, SPECIAL.3, SPECIAL.4 (P1), U$1.D4
unnamed: 9V_TO_5V.1, F.1
unnamed: COLOUR_SENSOR.3, U1.D6, _.10 (3A)
unnamed: COLOUR_SENSOR.4, U1.D7, _.15 (4A)
unnamed: RFID.4, U1.D12
unnamed: RFID.5, U1.D11
unnamed: RFID.6, U1.D13
unnamed: COLOUR_SENSOR.5, MULPLX.6, NANO.1, S_PWR.1, _.16 (VCC1)
unnamed: MOTOR1.2, _.3 (1Y)
unnamed: MOTOR1.3, _.6 (2Y)
unnamed: MOTOR2.2, _.11 (3Y)
unnamed: MOTOR2.3, _.14 (4Y)
unnamed: U1.D3, _.1 (1-2EN)
unnamed: U1.D2, _.7 (2A)
VIN: U1.VIN

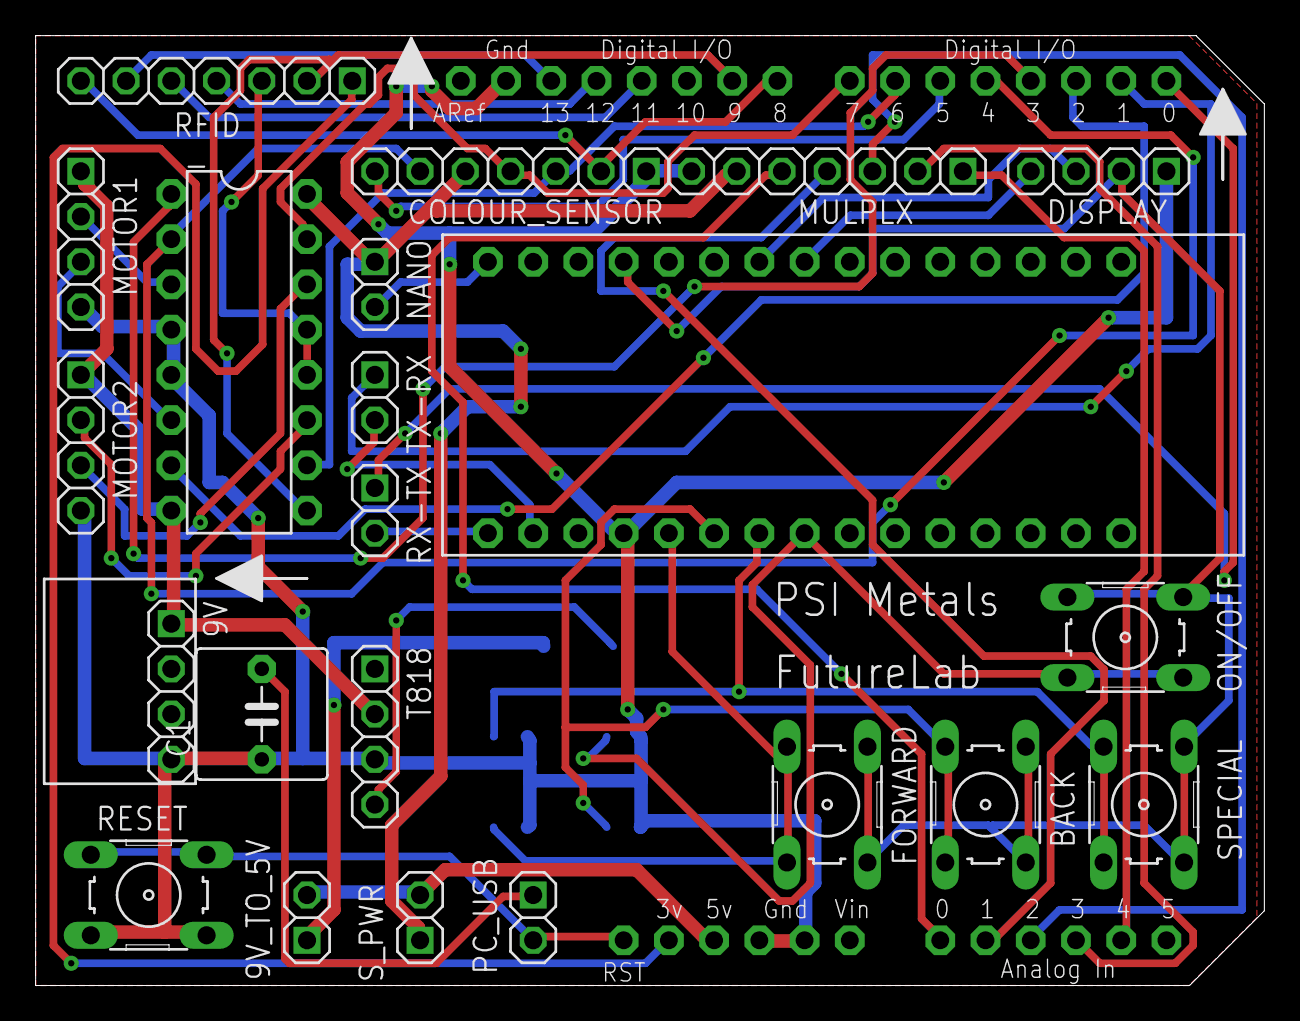
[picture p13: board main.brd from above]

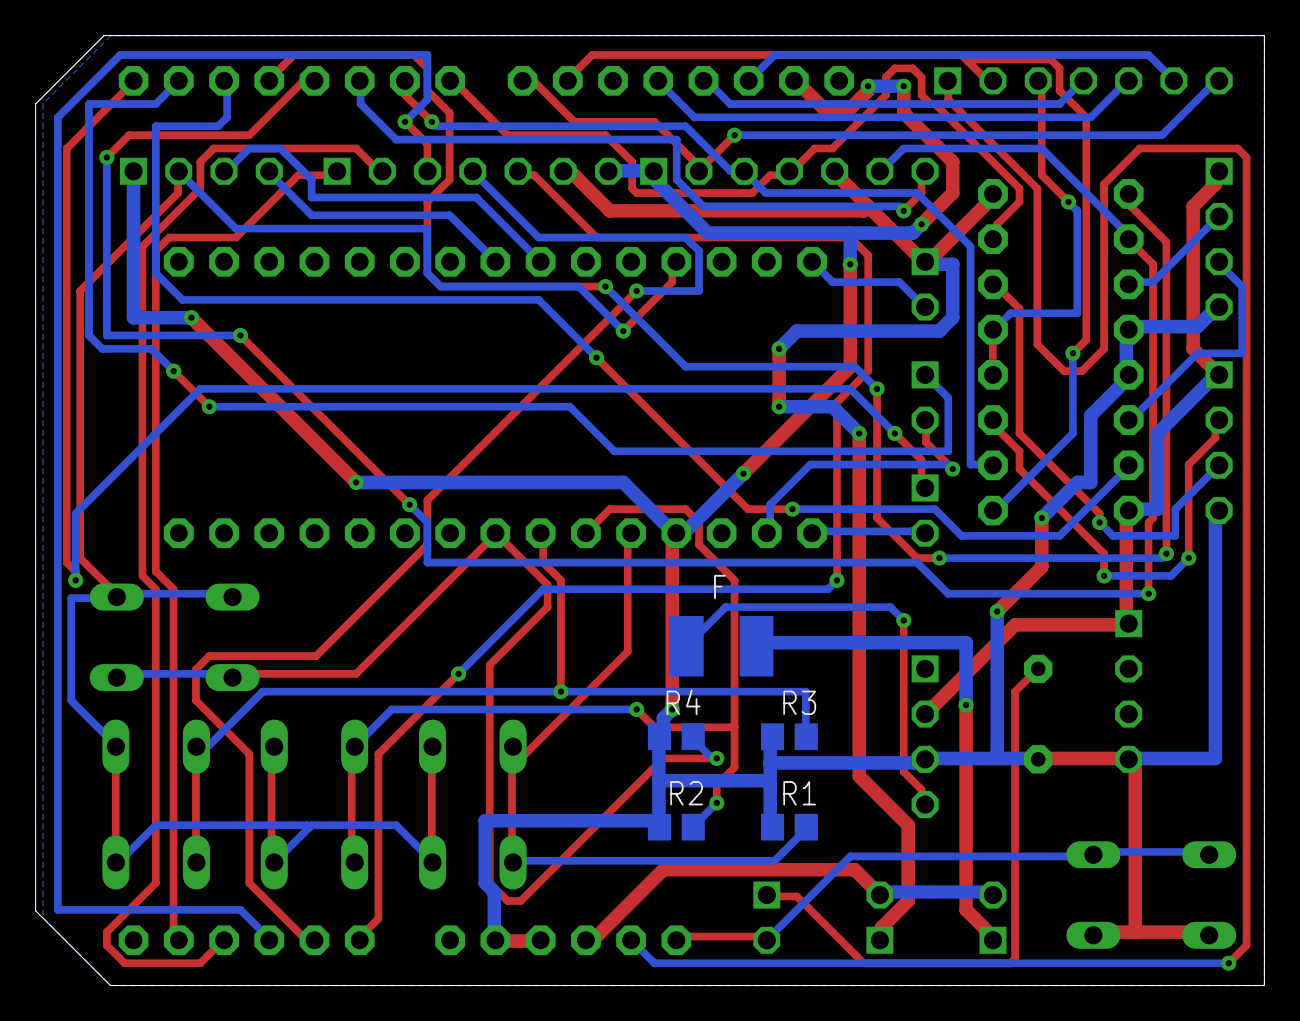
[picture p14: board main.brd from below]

Board: 2 copper layers, 69.0 x 53.3 mm, 28 parts (5 on the bottom side), 42 nets.

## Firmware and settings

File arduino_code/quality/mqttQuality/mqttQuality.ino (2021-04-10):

#include <SPI.h>

#include <Ethernet.h>

#include <PubSubClient.h>


// Update these with values suitable for your network.
byte mac[] = {
  0x72,
  0xB2,
  0xD0,
  0x0B,
  0x11,
  0x0D
};
//IPAddress ip(192,168,0,111);
//IPAddress server(192,168,0,102);
//IPAddress ip (169,254,166,102);
//IPAddress server (169,254,166,232);

//IPAddress ip (169,254,65,102);
//IPAddress server (169,254,65,51); 

IPAddress ip(192, 168, 0, 13);
IPAddress server(192, 168, 0, 21);

EthernetClient ethClient;
PubSubClient client(ethClient);

char speedArr[4]; // speed counts from 0 to 255
char * receivedMsg = (char * ) malloc(sizeof(char) * 2);
char * positionPointer = (char * ) malloc(sizeof(char) * 3);
char * button = (char * ) malloc(sizeof(char) * 2);

char command = 'n'; //nothing
boolean isManual = false;

//motor
int motor1_A = 2;
int motor1_B = 4;
int motor1_Speed = 3;

//default
int speed = 120;
char direction = 'r';
char started = '0';
bool writeInterval = false;

//vars
unsigned long startTime;
int interval;
char currRfid[9]; //use
char matPosition[8];
char currMatPosition[8];
unsigned long msgTimer = 0;
char quality[2];

bool isFirstOnTheTbl = false;
bool isAfterQCheck = false;
bool isUnloadingTblReady = false;
bool isDisplayProblemSent = false;
bool stopBeforeUnloading = false;
bool isMovingToUnload = false;
bool isCollectData = false;

int dCounter = 0;
int bCounter = 0;
int mCounter = 0;

void setup() {
  //memset(positionPointer, '\0', sizeof(positionPointer));
  strcpy(positionPointer, "ff\0");
  memset(matPosition, '\0', sizeof(matPosition));
  memset(receivedMsg, '\0', sizeof(receivedMsg));
  memset(button, '\0', sizeof(button));
  Serial.begin(115200);
  Serial.setTimeout(100); //communication with nano(display)

  //ir sensors
  pinMode(A0, OUTPUT); //1
  pinMode(A1, OUTPUT); //2
  pinMode(A2, OUTPUT); //3
  pinMode(A3, INPUT); //4
  //pinMode(A4,INPUT);//5
  //pinMode(A5,INPUT);//6
  //pinMode(5,INPUT);//7

  client.setServer(server, 1883);
  client.setCallback(callback);

  //Motor
  pinMode(motor1_A, OUTPUT);
  pinMode(motor1_B, OUTPUT);

  Ethernet.begin(mac, ip);

  // Allow the hardware to sort itself out
  delay(1500);
}
void reconnect() {
  // Loop until we're reconnected
  while (!client.connected() && !isManual) {
    //Serial.print("Attempting MQTT connection...");
    // Attempt to connect
    if (client.connect("arduinoQualityTable", "futurelab", "FutureLab123")) {
      //if (client.connect("arduinoQualityTable")) {
      //Serial.println("connected");
      // Once connected, publish an announcement...
      client.publish("/tables/connection", "arduinoQualityTable|connected");
      // ... and resubscribe

      client.subscribe("/quality/control");
      client.subscribe("/quality/MatRollInfo");
      client.subscribe("/quality/MatCheck");
      client.subscribe("/quality/MatReadyToUnloading");
      client.subscribe("/quality/MatMove");
      client.subscribe("/quality/MatCheckAuto");

    } else {
      //Serial.print("failed, rc=");
      //Serial.print(client.state());
      //Serial.println(" try again in 5 seconds");
      // Wait 5 seconds before retrying
      //delay(5000);
      for (int i = 0; i < 50; i++) {
        checkButtonInfo();
        if (isManual)
          break;
      }
    }
  }
}

void callback(char * topic, byte * payload, unsigned int length) {

  // Allocate the correct amount of memory for the payload copy
  byte * p = (byte * ) malloc(length);
  // Copy the payload to the new buffer
  memcpy(p, payload, length);

  //Serial.print("Message arrived [");
  //Serial.print(topic);
  //Serial.print("] ");
  if (strcmp(topic, "/quality/control") == 0) {
    bool isSpeed = false;
    for (int i = 0; i < length; i++) {
      //Serial.print((char)p[i]);

      if ((char) p[i] == 'l') //left
      {
        direction = 'l';
        client.publish("/quality/info", "direction|l");
      } else if ((char) p[i] == 'r') //right
      {
        direction = 'r';
        client.publish("/quality/info", "direction|r");
      } else if ((char) p[i] == 's') //start
      {
        motor(speed, direction);
        //started='1';
        client.publish("/quality/info", "isStarted|1");
      } else if ((char) p[i] == 'p') //pause
      {
        stopMotor();
        //started='0';
        client.publish("/quality/info", "isStarted|0");
      } else if ((char) p[i] == 't') //loopTime info
      {
        if (writeInterval == true)
          writeInterval = false;
        else
          writeInterval = true;

        //writeInterval = !writeInterval; //does not work

        if (writeInterval)
          client.publish("/quality/info", "loopTime|1");
        else
          client.publish("/quality/info", "loopTime|0");
      } else if ((char) p[i] == 'i') {
        writeInfo();
      } else {
        isSpeed = true;
      }
    }
    //Serial.println();

    if (isSpeed) {
      int power = 1;
      speed = 0;
      char temp;
      for (int i = length - 1; i >= 0; i--) {
        temp = ((char) p[i]);
        speed += atoi( & temp) * power;
        power *= 10;
      }

      if (speed < 100) //min
        speed = 100;
      if (speed > 255) //max
        speed = 255;

      //Serial.println(freeRam());
      //sprintf(speedArr, "%ld", speed); 
      //char* speedArrPointer = &speedArr[0]; 
      memset(speedArr, '\0', sizeof(speedArr));
      itoa(speed, speedArr, 10);
      char speedMsg[7] = "speed|\0";
      char * concSpeed = (char * ) malloc(20);
      memset(concSpeed, '\0', sizeof(concSpeed));
      strncpy(concSpeed, & speedMsg[0], sizeof(speedMsg)); /* copy name into the new var */
      strcat(concSpeed, & speedArr[0]); /* add the extension */
      client.publish("/quality/info", concSpeed);

      free(concSpeed);
    }
    //Serial.println();
  } else if (strcmp(topic, "/quality/MatRollInfo") == 0) {
    char warningLine[30] = "Received id is not correct.\0";
    if (length != 8) {
      if ('c' == (char) p[8]) //collect
      {
        isCollectData = true;
        for (int i = 0; i < 8; i++) {
          currRfid[i] = (char) p[i];
        }
        currRfid[9] = '\0';
      } else
        client.publish("/quality/warning", warningLine);
    }

    if (!isCollectData) {

      for (int i = 0; i < length; i++) {
        currRfid[i] = (char) p[i];
      }
      currRfid[9] = '\0';
      delay(1000);
      waitFeedback("rcd\0", 4);
      delay(500);
      waitFeedback(currRfid, 9);
      delay(1500);
      client.publish("/rolling/MatReadyToQCheck", currRfid);
      isFirstOnTheTbl = true;
      motor(speed, 'r');
      waitFeedback("pfq\0", 4);
      //go to center and wfq... then "/quality/MatCheck" received
    } else {
      waitFeedback("cdt\0", 4);
      isFirstOnTheTbl = true;
      motor(speed, 'r');
    }
  } else if (strcmp(topic, "/quality/MatCheck") == 0) {
    char warningLine[33] = "Received info is not correct.\0";
    char warningLineId[30] = "Received id is not correct.\0";
    bool isWritten = false;
    if (length != 10)
      client.publish("/quality/warning", warningLine);

    for (int i = 0; i < 8; i++) {
      if (currRfid[i] != (char) p[i]) {
        client.publish("/quality/warning", warningLineId);
        break;
      }
    }
    quality[0] = (char) p[9];
    quality[1] = '\0';
    char tmpQ[4];
    if (quality[0] == '0')
      tmpQ[0] = '1';
    else if (quality[0] == '1')
      tmpQ[0] = '0';
    else if (quality[0] == '2')
      tmpQ[0] = '0';

    tmpQ[1] = '0';
    tmpQ[2] = '0';
    tmpQ[3] = '\0';
    waitFeedback(tmpQ, 4);
    delay(4000);
    isAfterQCheck = true;
    //move to the end of the table
  } else if (strcmp(topic, "/quality/MatReadyToUnloading") == 0) {
    char warningLine[49] = "Received id is not correct. Expected: \0";
    bool isWritten = false;
    for (int i = 0; i < length; i++) {
      if ((char) p[i] != currRfid[i]) {
        if (!isWritten) {
          //strcpy(warningLine, "Received id is not correct. Expected: "); // copy name into the new var 
          strcat(warningLine, & currRfid[0]); // add the extension 
          client.publish("/quality/warning", warningLine);
          isWritten = true;
        }
      }
    }
    isUnloadingTblReady = true;
  } else if (strcmp(topic, "/quality/MatMove") == 0) {
    char warningLine[30] = "Received id is not correct.\0";
    if (length != 10)
      client.publish("/quality/warning", warningLine);

    if (!isCollectData) {
      for (int i = 0; i < 8; i++) {
        if (currRfid[i] != (char) p[i]) {
          client.publish("/quality/warning", warningLine);
          break;
        }
      }
    }

    if ((char) p[9] == 's') //to start pos
      movingStart();
    else if ((char) p[9] == 'e') //to end pos
      movingEnd();
  } else if (strcmp(topic, "/quality/MatCheckAuto") == 0) {
    client.publish("/colourSensor/MatReadyToQCheck", currRfid);
  }

  free(p);
}

void movingStart() {
  int beforeSensor = 1; //changeable
  motor(200, 'l');
  while (currMatPosition[beforeSensor] != '1') {
    checkPosition();
  }
  stopMotor();
  client.publish("/colourSensor/StartAutoQCheck", currRfid);
}

void movingEnd() {
  int afterSensor = 4; //changeable
  motor(200, 'r');
  while (currMatPosition[afterSensor] != '1') {
    checkPosition();
  }
  stopMotor();
  if (!isCollectData)
    client.publish("/colourSensor/MatEndQCheck", currRfid);
  else {
    client.publish("/colourSensor/MatEndQCheck", currRfid);
    waitFeedback("res\0", 4);
    waitFeedback("rdy\0", 4);
    isCollectData = false;
    memset(currRfid, '\0', sizeof(currRfid));
  }
}

void waitFeedback(char msg[], int msgSize) {
  long tmr = millis();
  for (int i = 0; i < 1; i++) //only 1 time
  {
    Serial.write(msg, msgSize);
    Serial.flush();
    while (receivedMsg[0] == '\0' && millis() - tmr < 10000)
      Serial.readBytes(receivedMsg, 2);
    if (receivedMsg[0] != '\0') {
      if (strcmp(receivedMsg, "r\0") == 0)
        memset(receivedMsg, '\0', sizeof(receivedMsg));

      while (Serial.available())
        Serial.read();
      return;
    } else if (!isDisplayProblemSent) {
      isDisplayProblemSent = true;
      client.publish("/quality/warning", "No display connected");
      waitFeedback(msg, msgSize);
    }
  }
  isDisplayProblemSent = false;

}

void checkButtonInfo() {
  Serial.readBytes(button, 2);

  if (strcmp(button, "f\0") == 0) {
    if (client.connected())
      client.disconnect();

    isManual = true;
    if (command != 'n' && command != 'o') //command=f,b,s
    {
      command = 'o';
      stopMotor();
    } else //command=n,o
    {
      command = 'f';
      motor(speed, 'r');
    }
  } else if (strcmp(button, "b\0") == 0) {
    if (client.connected())
      client.disconnect();

    isManual = true;
    if (command != 'n' && command != 'o') //command=f,b,s
    {
      command = 'o';
      stopMotor();
    } else //command=n,o
    {
      command = 'b';
      motor(speed, 'l');
    }
  } else if (strcmp(button, "s\0") == 0) {
    if (client.connected())
      client.disconnect();

    isManual = true;
    if (command != 'n' && command != 'o') //command=f,b,s
    {
      command = 'o';
      stopMotor();
    } else //command=n,o
    {

    }
  } else if (strcmp(button, "o\0") == 0) {
    if (client.connected())
      client.disconnect();

    if (command == 'n') {
      isManual = true;
      command = 'o';
    } else //command=f,b,s,o
    {
      isManual = false;
      command = 'n';
      stopMotor();
      //stopSpecial()
      Ethernet.begin(mac, ip);
      client.setServer(server, 1883);
      client.setCallback(callback);
      delay(1500);
    }
  }

  memset(button, '\0', sizeof(button));
}

void loop() {
  startTime = millis();
  checkButtonInfo();
  //Serial.println(freeRam());
  //server
  if (!client.connected() && !isManual) {
    reconnect();
  }
  client.loop();

  //after qcheck
  if (isAfterQCheck) {
    isAfterQCheck = false;
    waitFeedback("fwd\0", 4);
    delay(1000);
    speed = 100; //changeable (should be default)
    motor(speed, 'r');
    stopBeforeUnloading = true;
  }

  //transport to quality table
  if (isUnloadingTblReady) {
    isUnloadingTblReady = false;
    waitFeedback("rtu\0", 4);
    motor(speed, 'r');
    isMovingToUnload = true;
  }

  //ir sensors
  checkPosition();

  //write info loop time
  if (writeInterval) {
    interval = millis() - startTime;
    char intervalArr[7];
    itoa(interval, intervalArr, 10); // here 10 means decimal
    client.publish("/quality/loopTime", intervalArr);
    delay(100);
  }

}

int freeRam() {
  extern int __heap_start, * __brkval;
  int v;
  return (int) & v - (__brkval == 0 ? (int) & __heap_start : (int) __brkval);
}

void checkAction() {
  if (isFirstOnTheTbl) {
    if (currMatPosition[3] == '1')
      dCounter++;

    if (dCounter == 3) {
      stopMotor();
      dCounter = 0;
      isFirstOnTheTbl = false;
      if (!isCollectData) {
        waitFeedback("wfq\0", 4);
        delay(2000);
        client.publish("/quality/MatReadyToQCheck", currRfid);
      } else
        client.publish("/quality/MatReadyToQCheck", currRfid);
    }
  }

  if (stopBeforeUnloading) {
    if (currMatPosition[6] == '1') {
      bCounter++;
    }

    if (bCounter == 3) {
      stopMotor();
      bCounter = 0;
      stopBeforeUnloading = false;
      waitFeedback("wfu\0", 4);
      delay(1200);
      client.publish("/unloading/MatQualityInfo", currRfid);

    }
  }
  if (isMovingToUnload) {
    if (strstr(currMatPosition, "1") == NULL) {
      mCounter++;
    }

    if (mCounter == 3) {
      stopMotor();
      mCounter = 0;
      isMovingToUnload = false;
      client.publish("/quality/info", "QualityCheck is done.");
      delay(2000);
      waitFeedback("rdy\0", 4);
      memset(currRfid, '\0', sizeof(currRfid));
      delay(1000);
    }
  }

}

void checkPosition() {
  digitalWrite(A0, 0);
  digitalWrite(A1, 0);
  digitalWrite(A2, 0);
  if (digitalRead(A3) == 0)
    currMatPosition[0] = '1';
  else
    currMatPosition[0] = '0';

  digitalWrite(A0, 1);
  digitalWrite(A1, 0);
  digitalWrite(A2, 0);
  if (digitalRead(A3) == 0)
    currMatPosition[1] = '1';
  else
    currMatPosition[1] = '0';

  digitalWrite(A0, 0);
  digitalWrite(A1, 1);
  digitalWrite(A2, 0);
  if (digitalRead(A3) == 0)
    currMatPosition[2] = '1';
  else
    currMatPosition[2] = '0';

  digitalWrite(A0, 1);
  digitalWrite(A1, 1);
  digitalWrite(A2, 0);
  if (digitalRead(A3) == 0)
    currMatPosition[3] = '1';
  else
    currMatPosition[3] = '0';

  digitalWrite(A0, 0);
  digitalWrite(A1, 0);
  digitalWrite(A2, 1);
  if (digitalRead(A3) == 0)
    currMatPosition[4] = '1';
  else
    currMatPosition[4] = '0';

  digitalWrite(A0, 1);
  digitalWrite(A1, 0);
  digitalWrite(A2, 1);
  if (digitalRead(A3) == 0)
    currMatPosition[5] = '1';
  else
    currMatPosition[5] = '0';

  digitalWrite(A0, 0);
  digitalWrite(A1, 1);
  digitalWrite(A2, 1);
  if (digitalRead(A3) == 0)
    currMatPosition[6] = '1';
  else
    currMatPosition[6] = '0';

  currMatPosition[7] = '\0';

  checkAction();

  //Serial.println(millis() - msgTimer);
  if (strcmp(matPosition, currMatPosition) != 0 && currRfid[0] != '\0' && millis() - msgTimer > 200) //not eq
  {

    msgTimer = millis();
    char posMsg[19];
    memset(posMsg, '\0', sizeof(posMsg));
    strncpy(matPosition, currMatPosition, 8);
    strcat(posMsg, currRfid);
    strcat(posMsg, "|");
    char * currPositionPointer = getPositionInM(currMatPosition);

    if (currPositionPointer != NULL) {
      if (strcmp(currPositionPointer, positionPointer) != 0) {
        char * posMqtt = getPosMqtt(currPositionPointer);
        strncpy(positionPointer, currPositionPointer, 3);
        strcat(posMsg, posMqtt);
        strcat(posMsg, "\0");
        client.publish("/quality/MatPosition", posMsg);
        free(posMqtt);
      }
    } else {
      strcpy(positionPointer, "ff\0");
      strcat(posMsg, "-");
      strcat(posMsg, "\0");
      client.publish("/quality/MatPosition", posMsg);
    }
    free(currPositionPointer);
  }
}

char * getPosMqtt(char * currMatPosition) {
  char * arrMqttPos = (char * ) malloc(sizeof(char) * 10);
  if (strcmp(currMatPosition, "33\0") == 0) {
    strcpy(arrMqttPos, "33390\0");
    return arrMqttPos;
  } else if (strcmp(currMatPosition, "36\0") == 0) {
    strcpy(arrMqttPos, "35910\0");
    return arrMqttPos;
  } else if (strcmp(currMatPosition, "38\0") == 0) {
    strcpy(arrMqttPos, "37800\0");
    return arrMqttPos;
  } else if (strcmp(currMatPosition, "42\0") == 0) {
    strcpy(arrMqttPos, "41580\0");
    return arrMqttPos;
  } else if (strcmp(currMatPosition, "43\0") == 0) {
    strcpy(arrMqttPos, "43470\0");
    return arrMqttPos;
  } else if (strcmp(currMatPosition, "46\0") == 0) {
    strcpy(arrMqttPos, "45990\0");
    return arrMqttPos;
  } else if (strcmp(currMatPosition, "48\0") == 0) {
    strcpy(arrMqttPos, "47880\0");
    return arrMqttPos;
  }
}

char * getM(int i) {
  char * arrSm = (char * ) malloc(sizeof(char) * 3);
  if (i == 0) {
    arrSm[0] = '3';
    arrSm[1] = '3';
    arrSm[2] = '\0';
    return arrSm;
  } else if (i == 1) {
    arrSm[0] = '3';
    arrSm[1] = '6';
    arrSm[2] = '\0';
    return arrSm;
  } else if (i == 2) {
    arrSm[0] = '3';
    arrSm[1] = '8';
    arrSm[2] = '\0';
    return arrSm;
  } else if (i == 3) {
    arrSm[0] = '4';
    arrSm[1] = '2';
    arrSm[2] = '\0';
    return arrSm;
  } else if (i == 4) {
    arrSm[0] = '4';
    arrSm[1] = '3';
    arrSm[2] = '\0';
    return arrSm;
  } else if (i == 5) {
    arrSm[0] = '4';
    arrSm[1] = '6';
    arrSm[2] = '\0';
    return arrSm;
  } else if (i == 6) {
    arrSm[0] = '4';
    arrSm[1] = '8';
    arrSm[2] = '\0';
    return arrSm;
  }

}

char * getPositionInM(char currMatPosition[]) {
  for (int i = 6; i >= 0; i--) {
    if (currMatPosition[i] == '1') {
      return getM(i);
    }
  }
  return NULL;
}

void motor(int speed, char direction) {
  if (direction == 'l') //left
  {
    digitalWrite(motor1_A, 1);
    digitalWrite(motor1_B, 0);
  } else if (direction == 'r') //right
  {
    digitalWrite(motor1_A, 0);
    digitalWrite(motor1_B, 1);
  }
  analogWrite(motor1_Speed, speed); // speed counts from 0 to 255
  delay(20);
  started = '1';
}
void stopMotor() {
  analogWrite(motor1_Speed, 0);
  digitalWrite(motor1_A, 0);
  digitalWrite(motor1_B, 0);
  started = '0';
}

void writeInfo() {
  char * line = (char * ) malloc(sizeof(char) * 40);

  memset(line, '\0', sizeof(line));
  strcpy(line, "isStarted|"); // copy name into the new var 
  strcat(line, & started); // add the extension 
  line[11] = '\0'; //fix
  client.publish("/quality/motorInfo", line);

  memset(line, '\0', sizeof(line));
  strcpy(line, "direction|"); // copy name into the new var 
  strcat(line, & direction); // add the extension 
  line[11] = '\0'; //fix
  client.publish("/quality/motorInfo", line);

  //sprintf(speedArr, "%ld", speed);  
  memset(speedArr, '\0', sizeof(speedArr));
  itoa(speed, speedArr, 10); // here 10 means decimal
  memset(line, '\0', sizeof(line));
  strcpy(line, "speed|"); // copy name into the new var 
  strcat(line, & speedArr[0]); // add the extension 
  client.publish("/quality/motorInfo", line);

  free(line);

}

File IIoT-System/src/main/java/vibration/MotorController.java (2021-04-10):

package vibration;

import flink.Main;
import lombok.Getter;
import org.apache.log4j.Logger;
import org.eclipse.paho.client.mqttv3.MqttException;
import org.eclipse.paho.client.mqttv3.MqttMessage;
import topics.RollingTopic;

import java.nio.charset.StandardCharsets;


@Getter
public class MotorController implements Runnable {
    private static Logger logger = Logger.getLogger(MotorController.class);
    private boolean running = false;
    private volatile boolean rolling = false;
    private volatile boolean rollingTerminated = false;
    public double vibrationLimit = 0.3;
    private int anomalyCount = 0;

    @Override
    public void run() {

        logger.info("motor controller was started");


        if (Main.mqttClient.getClient() == null) {
            logger.error("Please init mqtt client in Main.class at first");
        } else {
            running = true;
            try {
                Main.mqttClient.getClient().subscribe(RollingTopic.MOTOR_INFO, (topic, message) -> {
                    String msg = new String(message.getPayload(), StandardCharsets.UTF_8);
                    //System.out.println("MSG:"+msg);
                    if (msg.startsWith("isRollingStarted")) {
                        rolling = msg.split("\\|")[1].equals("1");
                        //System.out.println("isRollingStarted:"+rolling);
                    }
                });


                while (running) {
                    //idel
                    Thread.sleep(100);
                }

            } catch (MqttException | InterruptedException e) {
                logger.error("problem during subscribing");
                logger.error(e);
            }
        }
    }


    public void checkAnomaly(double x, double y, double z) {
        if (!rollingTerminated) {
            double vibrationLvl = (Math.abs(x) + Math.abs(y) + Math.abs(z)) / 3.0;
            //System.out.println("vibrationLvl: "+vibrationLvl);
            if (rolling && Double.compare(vibrationLvl, vibrationLimit) < 0
                    && Double.compare(Main.xyzAvgDiff, vibrationLimit / 2.0) < 0) {
                anomalyCount++;
            } else {
                anomalyCount = 0;
            }
            if (anomalyCount > 1) {
                stopRolling();
                logger.error("ROLL WORKS INCORRECTLY");
                logger.error("STOP ROLLING");
                rollingTerminated = true;
                int waitSec = 10;
                new Thread(new Runnable() {
                    @Override
                    public void run() {
                        logger.info("Waiting before start rolling");
                        for (int i = waitSec; i > 0; i--) {
                            logger.info("Wait: " + i + " sec");
                            try {
                                Thread.sleep(1000);
                            } catch (InterruptedException e) {
                            }
                        }
                        logger.info("START ROLLING");
                        startRolling();
                        rollingTerminated = false;
                    }
                }).start();
            } else if (rolling) {
                logger.info("material is rolling");
            }
        }
    }

    public void startRolling() {
        try {
            Main.mqttClient.getClient().publish(RollingTopic.CONTROL,
                    new MqttMessage(("m").getBytes(StandardCharsets.UTF_8)));
            Main.mqttClient.getClient().publish(RollingTopic.CONTROL,
                    new MqttMessage(("s").getBytes(StandardCharsets.UTF_8)));
        } catch (MqttException e) {
            logger.error("problem during startRolling");
            logger.error(e);
        }
    }

    public void stopRolling() {
        try {
            Main.mqttClient.getClient().publish(RollingTopic.CONTROL,
                    new MqttMessage(("z").getBytes(StandardCharsets.UTF_8)));
            Main.mqttClient.getClient().publish(RollingTopic.CONTROL,
                    new MqttMessage(("p").getBytes(StandardCharsets.UTF_8)));
        } catch (MqttException e) {
            logger.error("problem during stopRolling");
            logger.error(e);
        }
    }

    private void close() {
        running = false;
    }
}

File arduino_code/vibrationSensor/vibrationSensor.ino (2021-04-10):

#include <Ethernet.h>

#include <Adafruit_LIS3DH.h>

#include <Adafruit_Sensor.h>

#include <PubSubClientColour.h>


// I2C
Adafruit_LIS3DH lis = Adafruit_LIS3DH();
byte mac[] = {
  0x3E,
  0x8A,
  0x53,
  0xAA,
  0x09,
  0xCE
};

IPAddress ip(192, 168, 0, 16);
IPAddress server(192, 168, 0, 21);

EthernetClient ethClient;
PubSubClientColour client(ethClient);

bool isWorking = true;
//bool posReseived = false;
byte motorInfoReceived[5]; //0 or 1
byte location = 0;
byte sensor_id = 0;
byte motor_state[5]; //0 or 1
byte motor_speed[5]; //0 .. 255
char motor_direction[5]; //r or l
char pos[5];
unsigned long msgTimer = 0;

/*
 * location:
 * 0 = loading table
 * 1 = rolling table
 * 2 = roll
 * 3 = quality table
 * 4 = unloading table
 */

/*
 * motors:
 * 0 = loading table
 * 1 = rolling table
 * 2 = roll
 * 3 = quality table
 * 4 = unloading table
 */

byte loading_table = 0;
byte rolling_table = 1;
byte roll = 2;
byte quality_table = 3;
byte unloading_table = 4;

char * topicCat = (char * ) malloc(45);
char loading_t[] = "/loading\0";
char rolling_t[] = "/rolling\0";
char quality_t[] = "/quality\0";
char unloading_t[] = "/unloading\0";
char vibration_s[] = "/arduinoVibrationSensor\0";

void setup(void) {

  memset(topicCat, '\0', sizeof(topicCat));
  memset(pos, '0', sizeof(pos));
  memset(motorInfoReceived, 0, sizeof(motorInfoReceived));
  memset(motor_state, 0, sizeof(motor_state));
  memset(motor_speed, 0, sizeof(motor_speed));
  memset(motor_direction, '\0', sizeof(motor_direction));
  Serial.begin(115200);

  if (!lis.begin(0x18)) { // change this to 0x19 for alternative i2c address
    Serial.println("Couldnt start");
    while (1);
  }

  lis.setRange(LIS3DH_RANGE_2_G); // 2, 4, 8 or 16 G

  Serial.print("Range = ");
  Serial.print(2 << lis.getRange());
  Serial.println("G");

  client.setServer(server, 1883);
  client.setCallback(callback);

  Ethernet.begin(mac, ip);

  // Allow the hardware to sort itself out
  delay(1500);
}

void reconnect() {
  // Loop until we're reconnected
  while (!client.connected()) {

    memset(topicCat, '\0', sizeof(topicCat));
    strcpy(topicCat, vibration_s);
    memmove( & topicCat[0], & topicCat[1], strlen(topicCat)); //del "/"

    if (client.connect(topicCat, "futurelab", "FutureLab123")) { // "arduinoVibrationSensor"

      strcat(topicCat, "|connected"); // "arduinoVibrationSensor|connected"
      client.publish("/tables/connection", topicCat);

      memset(topicCat, '\0', sizeof(topicCat));
      strcpy(topicCat, vibration_s);
      strcat(topicCat, "/control");
      client.subscribe(topicCat); // "/arduinoVibrationSensor/control"

      memset(topicCat, '\0', sizeof(topicCat));
      strcpy(topicCat, vibration_s);
      strcat(topicCat, "/data");
      client.subscribe(topicCat); // "/arduinoVibrationSensor/data"

      memset(topicCat, '\0', sizeof(topicCat));
      strcpy(topicCat, loading_t);
      strcat(topicCat, "/motorInfo");
      client.subscribe(topicCat); // "/loading/motorInfo"

      memset(topicCat, '\0', sizeof(topicCat));
      strcpy(topicCat, rolling_t);
      strcat(topicCat, "/motorInfo");
      client.subscribe(topicCat); // "/rolling/motorInfo"

      memset(topicCat, '\0', sizeof(topicCat));
      strcpy(topicCat, quality_t);
      strcat(topicCat, "/motorInfo");
      client.subscribe(topicCat); // "/quality/motorInfo"

      memset(topicCat, '\0', sizeof(topicCat));
      strcpy(topicCat, unloading_t);
      strcat(topicCat, "/motorInfo");
      client.subscribe(topicCat); // "/unloading/motorInfo"

      memset(topicCat, '\0', sizeof(topicCat));
      strcpy(topicCat, loading_t);
      strcat(topicCat, "/MatPosition");
      client.subscribe(topicCat); // "/loading/MatPosition"

      memset(topicCat, '\0', sizeof(topicCat));
      strcpy(topicCat, rolling_t);
      strcat(topicCat, "/MatPosition");
      client.subscribe(topicCat); // "/rolling/MatPosition"

      memset(topicCat, '\0', sizeof(topicCat));
      strcpy(topicCat, quality_t);
      strcat(topicCat, "/MatPosition");
      client.subscribe(topicCat); // "/quality/MatPosition"

      memset(topicCat, '\0', sizeof(topicCat));
      strcpy(topicCat, unloading_t);
      strcat(topicCat, "/MatPosition");
      client.subscribe(topicCat); // "/unloading/MatPosition"

    } else {
      // Wait 5 seconds before retrying
      delay(5000);
    }
  }
}

void callback(char * topic, byte * payload, unsigned int length) {

  // Allocate the correct amount of memory for the payload copy
  byte * p = (byte * ) malloc(length);
  // Copy the payload to the new buffer
  memcpy(p, payload, length);

  memset(topicCat, '\0', sizeof(topicCat));
  strcpy(topicCat, vibration_s);
  strcat(topicCat, "/control");

  if (strcmp(topic, topicCat) == 0) // "/arduinoVibrationSensor/control"
  {
    for (int i = 0; i < length; i++) {
      //Serial.print((char)p[i]);

      if ((char) p[i] == 's') //start
      {
        isWorking = true;
        memset(topicCat, '\0', sizeof(topicCat));
        strcpy(topicCat, vibration_s);
        strcat(topicCat, "/info");
        client.publish(topicCat, "started");
      } else if ((char) p[i] == 'p') //pause
      {
        isWorking = false;
        memset(topicCat, '\0', sizeof(topicCat));
        strcpy(topicCat, vibration_s);
        strcat(topicCat, "/info");
        client.publish(topicCat, "stopped");
        memset(pos, '0', sizeof(pos));
        memset(motorInfoReceived, 0, sizeof(motorInfoReceived));
        memset(motor_state, 0, sizeof(motor_state));
        memset(motor_speed, 0, sizeof(motor_speed));
        memset(motor_direction, '\0', sizeof(motor_direction));
      }
    }

    free(p);
    return;
  }

  memset(topicCat, '\0', sizeof(topicCat));
  strcpy(topicCat, vibration_s);
  strcat(topicCat, "/data");

  if (strcmp(topic, topicCat) == 0) //1 byte = location, 2 byte = sensor_id, topic =  "/arduinoVibrationSensor/data"
  {
    isWorking = true;
    location = p[0] - 48; //ascii transform
    sensor_id = p[1] - 48;

    memset(pos, '0', sizeof(pos));
    memset(motorInfoReceived, 0, sizeof(motorInfoReceived));
    memset(motor_state, 0, sizeof(motor_state));
    memset(motor_speed, 0, sizeof(motor_speed));
    memset(motor_direction, '\0', sizeof(motor_direction));

    free(p);
    return;
  }

  //MOTOR__INFO

  memset(topicCat, '\0', sizeof(topicCat));
  strcpy(topicCat, loading_t);
  strcat(topicCat, "/motorInfo");
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
